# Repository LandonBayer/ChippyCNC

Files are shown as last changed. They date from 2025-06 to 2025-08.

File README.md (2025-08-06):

# Chippy
CNC Mills are expensive, large, and generally not very accessible to the average maker in their home. With Chippy, a small, simple, cheap but powerful CNC router, these capabilities may become available to the hobbiest at a relatively low price. Unlike the commonly found [3018-style](https://a.co/d/4NDyeWJ) cnc, which is a respectable $150 but fails to do anything more than engraving, Chippy boasts linear rails rather than guides, ball screws in place of lead screws, a 500W ER16 spindle, and an extrusion frame to maximize performance. Even the similarly priced Lunyee [3018-pro](https://a.co/d/8d0D7FV) still uses guides and lead screws in place of high quality parts, making Chippy a more compelling DIY package.

I personally had a lot of experience using CNC machines through my robotics team, where I regularly ran an [Omio X8-2200L](https://www.omiocnc.com/products/x8-series/x8-2200l-usb-cnc-desktop-engraver.html) to manufacture parts. Using that experience, I designed Chippy to best compromise performance, ease of use, and reliability in the ways I sought throughout the build seasons. I also did my best to use some parts that I had on hand, such as the linear rails, ball screws (without nuts), a Z stage, and 8020 extrusion. This minimizes my personal input cost, as well as recycles otherwise useless components that I own.

Project Goals:
 - Create a usable but cheap CNC
 - Small footprint (small volume will encompass most parts)
 - Functional speeds, expected to be slow but reasonable
 - Minimum Z probing, ideally X and Y as well
 - Rigid Frame
 - Effective clamping solution
 - Be able to mill aluminum (not just engrave, and not only wood/plastics)

Specs:
- 200 x 180 x 90mm working area (more on the sides for clamping)
- Linear rails to maximize rigidity
- Ball screws to maximize accuracy (not found on any other low cost machines)
- All aluminum frame
- 500 Watt 12000 RPM ER16 spindle
- GRBL Control (outdated but will function perfectly in most scenarios)
- High torque stepper motors on all axis
- Option to switch between a wooden spoilboard for plate work and a machinist vice for 3D parts (note: I can't find exact dimensions on the vice, so that will be added at a later date)
- Integrated E-stop

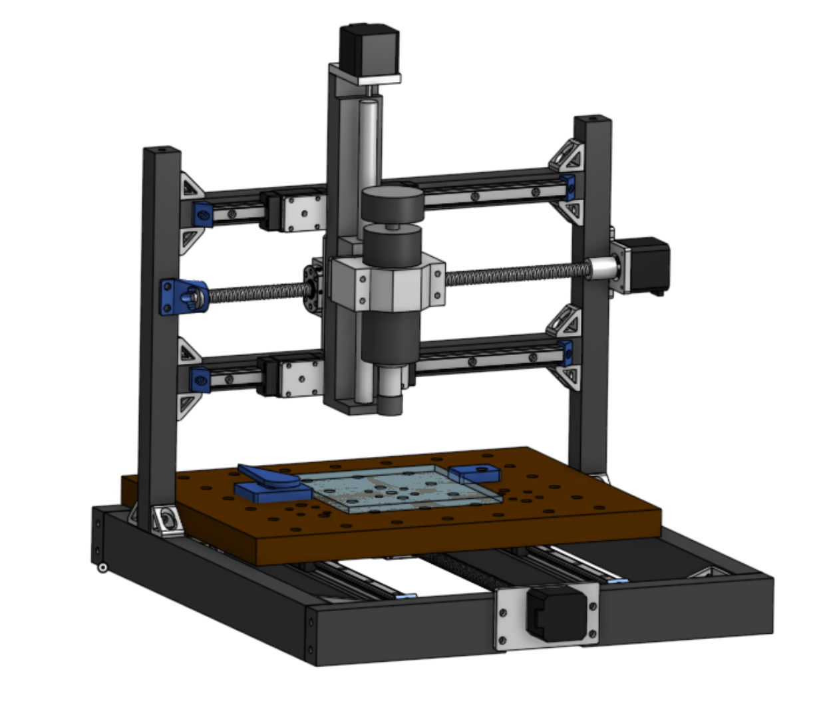
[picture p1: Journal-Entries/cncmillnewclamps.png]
finalscreenshot


[final]: Journal-Entries/cncmillnewclamps.png

[Onshape Link](https://cad.onshape.com/documents/fe491084e56455da2d5a649d/w/3d810b1fec2b376e1d8655d1/e/08e152ea0122b69bfa13cece)

[BOM Link](https://docs.google.com/spreadsheets/d/1udPoCN8MQFdChB4r3Y68Km0VLGHvW1hfCCyUqifvbzs/edit?usp=sharing)

Here's a rough wiring diagram of how to put this machine together, as per Hack Club requirements:

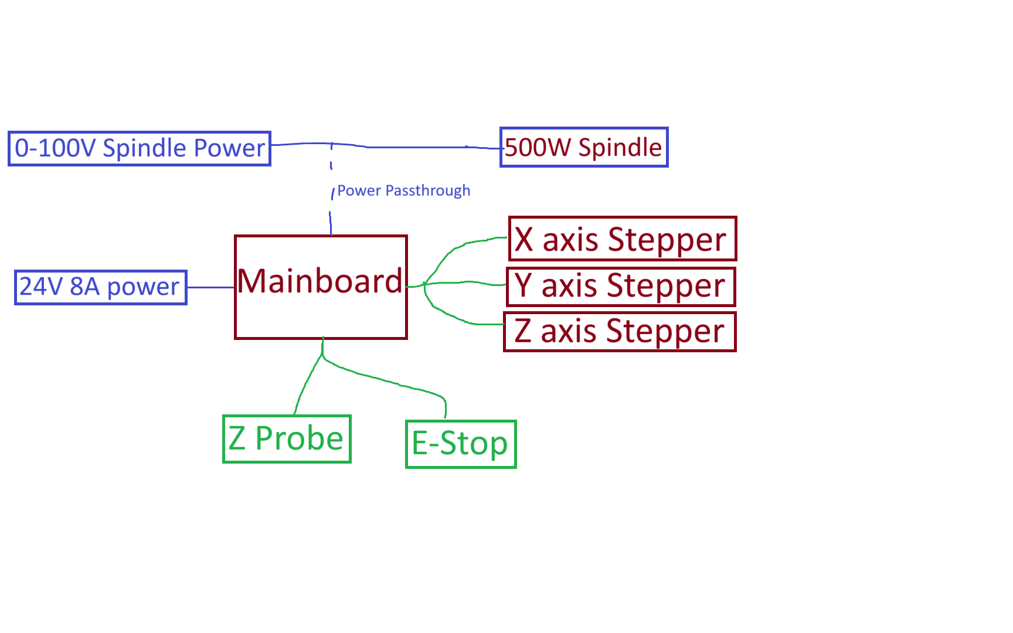
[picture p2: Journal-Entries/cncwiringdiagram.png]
wiringdiagram


[wires]: Journal-Entries/cncwiringdiagram.png

| ITEM | PRICE | QUANTITY | TOTAL PRICE | SOURCE | Ordered | Owned | LINK |
| --- | --- | --- | --- | --- | --- | --- | --- |
| Mainboard | 19.57 | 1 | 19.57 | Aliexpress | FALSE | FALSE | https://www.aliexpress.us/item/3256805662918330.html |
| 400mm ball screw | 22.1 | 2 | 44.2 | Aliexpress | FALSE | FALSE | https://www.aliexpress.us/item/3256802936754324.html |
| ball screw nut mounting block | 4.76 | 2 | 9.52 | Aliexpress | FALSE | FALSE | https://www.aliexpress.us/item/2255800872193882.html |
| Daedalus CNC Spindle Motor Kit, 500w, ER16, Brushed | 99.99 | 1 | 99.99 | Amazon | FALSE | FALSE | https://a.co/d/ilFF7XH |
| 24V 8A power supply (for steppers + control) | 16.99 | 1 | 16.99 | Amazon | FALSE | FALSE | https://a.co/d/3KXWlDU |
| Nema 17 2 amp high torque stepper motors (3 pack) + wires | 32.99 | 1 | 32.99 | Amazon | FALSE | FALSE | https://a.co/d/6JUlACn |
| 5mmx8mm coupler | 6.58 | 1 | 6.58 | Aliexpress | FALSE | FALSE | https://www.aliexpress.us/item/3256807349420029.html |
| Z touch probe | 6.42 | 1 | 6.42 | Aliexpress | FALSE | FALSE | https://www.aliexpress.us/item/3256808663692081.html |
| 3 inch cnc vice + mounting bolts | 44.77 | 1 | 44.77 | Amazon | FALSE | FALSE | https://a.co/d/5kOnS3H |
| E-stop and Limit Switch Kit | 9.78 | 1 | 9.78 | Aliexpress | FALSE | FALSE | https://www.aliexpress.us/item/3256807406356837.html |
| M4 T-nuts for the linear rails (3030 sized work for 1x1 extrusion) | 6.39 | 1 | 6.39 | Amazon | FALSE | FALSE | https://a.co/d/hFEOWDT |
| M10 3pack 25mm pins (for clamping) | 4.9 | 2 | 9.8 | Aliexpress | FALSE | FALSE | https://www.aliexpress.us/item/3256805291847458.html |
| Ball screw support bearings (10mm ID) | 3.32 | 1 | 3.32 | Aliexpress | FALSE | FALSE | https://www.aliexpress.us/item/3256808665674212.html |
| Ball screw support bearings (8mm ID) | 2.99 | 1 | 2.99 | Aliexpress | FALSE | FALSE | https://www.aliexpress.us/item/3256805324873222.html |
|  |  |  |  |  |  |  |  |
| Assorted Metric screws (mostly for M4, I have these already) | 17.83 | 1 | 17.83 | Amazon | FALSE | TRUE | https://a.co/d/3Fa4UwA |
| 90 degree 8020 brackets + bolts (can be used in place of 2x2 ones as well) | 18.9 | 3 | 56.7 | Amazon | FALSE | TRUE | https://a.co/d/7QSxBpf |
| Z stage (recommended 100mm, I had 200mm) | 55.98 | 1 | 55.98 | Amazon | FALSE | TRUE | https://a.co/d/2d2hLF8 |
| 350mm HGH15 linear rails (by far the most expensive part) | 89.92 | 2 | 179.84 | Aliexpress | FALSE | TRUE | https://www.aliexpress.us/item/3256801410951679.html |
| 450mm 2x1" 8020 extrusion (cut to length) | 14.51 | 3 | 43.53 | Other | FALSE | TRUE | https://8020.net/1020.html |
| 450mm 1x1" 8020 extrusion (cut to length) | 9.5 | 2 | 19 | Other | FALSE | TRUE | https://8020.net/1010.html |
| 200mm 2x1" 8020 extrusion (cut to length) | 7.73 | 2 | 15.46 | Other | FALSE | TRUE | https://8020.net/1020.html |
| 400mm 1x1" 8020 extrusion (cut to length) | 8.76 | 2 | 17.52 | Other | FALSE | TRUE | https://8020.net/1010.html |
| 350mm 1x1" 8020 extrusion (cut to length) | 7.97 | 2 | 15.94 | Other | FALSE | TRUE | https://8020.net/1010.html |
| 1kg PLA Pro filament (for clamps and mounting plates if desired) | 24.99 | 1 | 24.99 | Other | FALSE | TRUE | https://us.polymaker.com/products/polylite-pla-pro?variant=39574346334265 |
| 6mm shank 2mm ball NO 3D Probe | 52.35 | 1 | 52.35 | Aliexpress | FALSE | FALSE | https://www.aliexpress.us/item/3256808425022835.html |
|  |  | Necessary total: | 737.82 |  |  |  |  |
|  |  | My total: | 310.6 |  |  |  |  |
|  |  | With probe: | 362.95 |

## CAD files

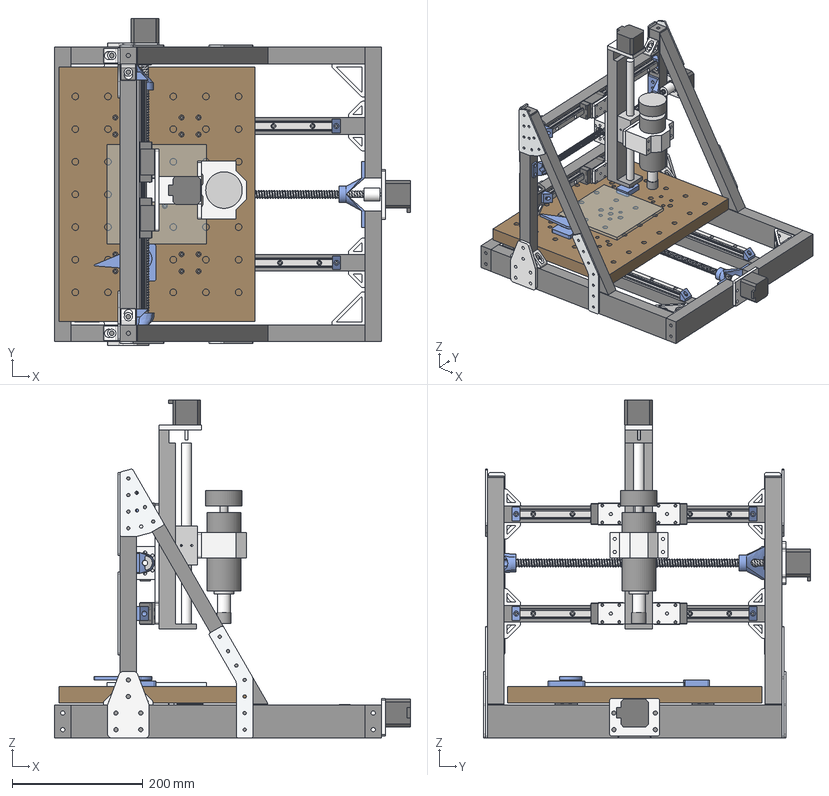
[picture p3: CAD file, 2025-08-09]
CAD-Chippy.step
545.1 x 501.5 x 517.5 mm
Rail End Stop x 8
47065T663_Silver Gusset Bracket x 20
10mm ID Bearing (double) x 2
Y axis rail Extrusion Right
Y axis rail Extrusion Left
X Motor Bearing Support
Base Extrusion Left
Y axis Bearing Support
5mmx8mm Shaft Coupler x 2
Clamping Dowel x 2
2x2 Corner Bracket x 4
Clamping Cam
1 in. 150 Deg. Gusset (am-4165) x 2
Z Mount Plate
Angle Stabilizing Extrusion x 2
NEMA 17 17HE15-1504S v5 x 3
Static Spacer Clamping Block
Spoilboard
1 in. 30 Degree Gusset (am-4160) x 2
Horizontal Extrusion Bottom
Base Extrusion Front Right
X axis Motor Mount Plate
1 in. Tee Gusset (am-4158 ) x 4
Vertical Extrusion Left
Base Extrusion Back
Base Plate Front
Y Motor Bearing Support
400mm ball screw x 2
Ball Screw Nut Housing Block x 2
92029A100 x 8
SFU1204 Nut v1 x 4
X axis Bearing Support
Moving Spacer Clamping Block
Spindle
Spindle Clamp
[Z] HGR15R x 4
[Z] HGH15CA x 8
8mm ID Bearing x 2
Base Extrusion Right
The Mega Z Mount plate
Vertical Rigidity Plate x 2
Vertical Extrusion Right
Base Extrusion Front Left
Stock
Motor Mount (3dp)
Mounting Block
16mm OD ball screw
Horizontal Extrusion Top

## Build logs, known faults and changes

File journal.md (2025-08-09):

---
title: "Chippy CNC"
author: "LandonBayer"
description: "Designing and building a cheap CNC mill using as many random parts I have as possible to minimize cost"
created_at: "2025-05-25"
---
Total time spent: 31 hours

## **5/25/2025 Log 1: Initial Concepts**

I began by trying to figure out if this is even possible. To get my ideas flowing, I made a quick [Google doc](https://docs.google.com/document/d/1eDa18zaTmOcg4O9jXUVwCgunUB5oY8t1EJznX5E89rA/edit?usp=sharing ) with each part of the CNC as I thought of them and explained how I would fulfill that requirement: either with parts I have or links to a cheap option I could use.

I set up this repo, made an [Onshape document](https://cad.onshape.com/documents/fe491084e56455da2d5a649d/w/3d810b1fec2b376e1d8655d1/e/48dd41e2a4bf65c8f3ef253b), and my research document above. I'm doing my best to fit into the $150 price tag to avoid the extra bar for $350 funding, but I may apply for it as necessary in the future. It would certainly be a huge upgrade to the machine, but the goal is a minimum functioning product for as little as possible. 

I'm looking to follow a basic CNC configuration with the spindle moving in XZ and the bed in Y, much like a bedslinger 3D printer or a 3018 style CNC.  

Time Spent: 45 Minutes (mostly research)

## **5/25/2025 Log 2: Ideation**

Some parts are not in my house at this exact moment so I need to wait a few days to go and grab them. In the meantime, I'll try to design most of the printer and be able to swap out the CAD models as I get the real ones and create/find models for them.

It is also worth noting that I have access to an Omio CNC router through my robotics team, which will enable me to make custom parts in aluminum or polycarbonate as I please (though I may have to buy stock as part of my budget). I also recently set up a 4th axis on it, so I can even do some more complex parts too.

Here are some sources of inspiration:

Cubiko CNC
3018 CNC

Time Spent: 15 Minutes

## **5/26/2025 Log 3: More Research**

I can't get some of the parts that I need until tomorrow, so I'm mostly holding off on CAD work until then to avoid extra work. In the meantime, I'm continuing to look into how I'm going to put this all together. I'm currently examining [GRBL-Mega](https://github.com/gnea/grbl-Mega), since I have an Arduino Mega with some sort of motor driver hat that hopefully is compatible. I also have a random Raspberry Pi 3B that I could use as a standalone computer for the CNC (just so it doesn't have to sit next to my real computer).
I'm doing as much pre-requisitve research as possible while I wait for those parts and so I don't waste time doing something that isn't possible (or I know where to put more of my budget). So far, the main budget items I have planned for are a spindle (cheapest one I could find is $27, the 3018 type spindle with an ER11 collet), a fixture table that I will likely make myself on the Omio CNC, stepper motors, and possibly a second ball screw of the same model I already have (~60, comes with a motor). Again, I'm hoping to stay under $150 but I may expand beyond that to accomodate any necessary parts for the functioning of the machine, or add more features like probing, an enclosure, or a better spindle.

Time spent: 45 Minutes

## **6/02/2025 Log 4: Finding Parts**

Most of this past week, I've been busy with the end of the school year, but I still took some time to get together all the parts I currently have and what needs to be purchased. To recap, I have two 400mm ball screws without nuts, four 350mm HGH15 linear rails, a RATTMMOTOR CBX 1605-200mm Z axis without a motor, and have since determined that the Arduino Mega with the Reprap RAMPS V1.4 sheild I have will not work as it is more suited for 3D printers and doesn't have the power to run a spindle. With these decisions, I am currently leaning toward [this](https://www.aliexpress.us/item/3256805662918330.html) control board, two of [these](https://www.aliexpress.us/item/3256807902881311.html) ball nuts, and finally [this](https://a.co/d/bSWRW8X) power supply and spindle combo, which I know will be compatible with the chosen control board.

parts I have

[parts]: Journal-Entries/parts.jpg

Of these, my biggest concern is the spindle, as it is quite small and has a high risk of lacking rigidity. I really just want this to function, so even if it is very slow or only mills soft materials, I'll be happy and can expand upon it later. The total cost for these parts is around $105, leaving me only $45 left in my budget to purchase any other components like the stepper motors, structural hardware, limit switches, wiring, and other necessary components like shaft couplers, bolts, etc. Because of this, alongside the potential for a significantly more powerful machine by spending just slightly more, I am likely going to propose my project to the $350 budget range in order to make this viable.

Time spent: 1 hour (over the week)

## **6/03/2025 Log 5: Beginning Design**

Given that I'm starting with many parts on hand, I'm getting 3D models of them where possible. I was able to find a model for the [spindle](https://www.thingiverse.com/thing:4856147), [linear rails](https://grabcad.com/library/hgh15ca-hgr15r-1), and [ball screw nuts](https://grabcad.com/library/sfu1204-ballscrew-nut-22mm-1). I also whipped up a model for the lead screw in Onshape using a helix curve and a sweep toolpath with a 2.5mm circle and a 5mm pitch helix. Unfortunately, this mainly leaves the Z stage without a model, of which I may need to replicate myself. To minimize the amount of CAD work to be done, I only plan to model the block (nut) on the screw, since those mounting features are the only part of the assembly that I really care about, alongside the back of it which has rails with captive nuts for mounting. With these parts accounted for, I'll now move into more modeling of the machine, based around a few design constraints: the parts I have, using 8020 for structural pieces where possible, and doing any custom parts based on 1/4" plate as I have access to it in small quantities.

Separately, I've tentatively decided on [this](https://a.co/d/2pTGfU2) 3-pack of NEMA 17 stepper motors that should be compatible with the control board as well and are quite cheap at $26 for all three. I have added the associated [3D model](https://grabcad.com/library/nema-17-17he15-1504s-1) to my Onshape document as well.

Time spent: 1 hour

## **6/04/2025 Log 6: Base sketches**

I did out some sketches in Onshape, making this as parametric as possible. I'm using some variables to name certain values like the length of my rails, ball screws, and the gap between the table and the spindle (Z-gap). I'm taking the time to think through these sizes and constraints to ensure they will propogate down correctly later on if I need to change things. I also made a small subassembly for the linear rails with limited slider mates on the blocks.

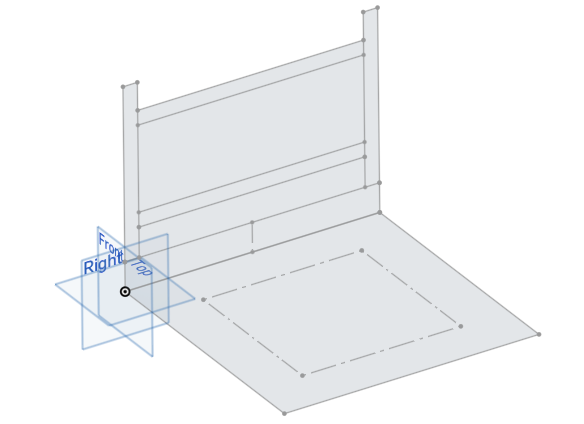
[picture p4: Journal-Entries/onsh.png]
onshape


[def]: Journal-Entries/onsh.png

Time spent: 30 minutes

## **6/16/2025 Log 7: More Onshape**

I worked out the back of the mill, which is the X axis and will hold the Z axis on it. I'm starting very simple, with some 8020 extrusions going around and some 2x1 ones at the bottom to give me some space for the rails and ball screw on the Y axis. My main issue with this was that the 8020 featurescript in Onshape is really difficult to use, as it generates facing straight up all the time. I spent quite a while trying to figure out a workaround and eventually settled on a not-ideal but somewhat parametric way to get the lengths set in the part studio.

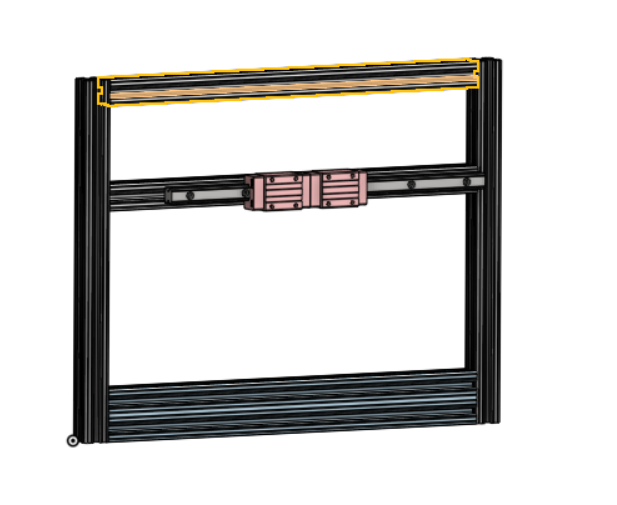
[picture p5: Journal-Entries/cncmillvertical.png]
cncmillvertical


[vert]: Journal-Entries/cncmillvertical.png

Time spent: 1.5 hours

## **6/17/2025 Log 8: Onshape Struggles Continue**

As I build out the rest of the machine in Onshape, I am beginning to really hate the 8020 featurescript and even using it as a part in CAD. Since it has rounded corners, I cannot add mate connectors to the corners exactly and instead have to use some strange face mates to connect the pieces. After discussing these issues with another Hack Club member, he recommended I simply model the 8020 as a solid 1x1 inch box, which I will convert now before the design gets too large. This means I will basically have to re-do both the part studio and assembly, but it will make things much easier going forward. You can also see some corner braces and attachment methods being added, though they aren't completely cadded in yet. I have some small 1x1 corner brackets, large 2x2 brackets for the inside of the base, and square pieces that are meant to attach three tapped 8020 extrusions in the corners (more details to come). Let's get to the conversion!

Before pic:

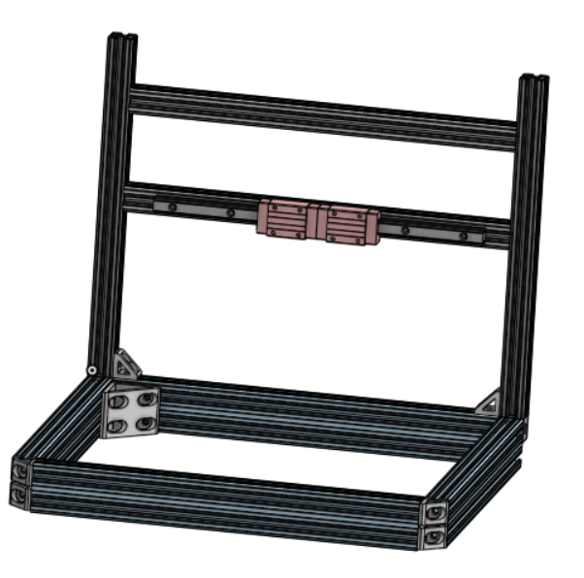
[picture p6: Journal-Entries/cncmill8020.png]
cncmill8020


[eightytwenty]: Journal-Entries/cncmill8020.png

Time spent: 1 hour

## **6/18/2025 Log 9: Onshape grind + Rethinking the machine**

I'd like to touch on that rethinking part first: I was initially trying to hit the $150 price point Hack Club offers, but after reviewing the guidelines more closely, I believe this is likely to fall into the advanced $350 category. For this reason, I'm looking at possible changes to my spindle (easiest) or even to the control board, drivers and motors (harder). The spindle is a straightforward upgrade with the same controller up to a 500W spindle, which makes it an ideal easy solution. However, the main limiting factor at this point would be the stepper motors I'm using to drive the whole machine, which are limited to 2 amps of maximum current based on the A4988 drivers the control board has. If I choose a different control board without integrated drivers, I could increase the power of those drivers up to 4A or higher, giving me room to put on larger stepper motors that will make the machine run much better. I will be continuing to consider this option as I move forward with the design, as it should not be heavily reliant on this choice.

As for Onshape, now comes the time to re-do all the 8020 extrusions to be simple boxes for ease of design. Here is what it looks like after:

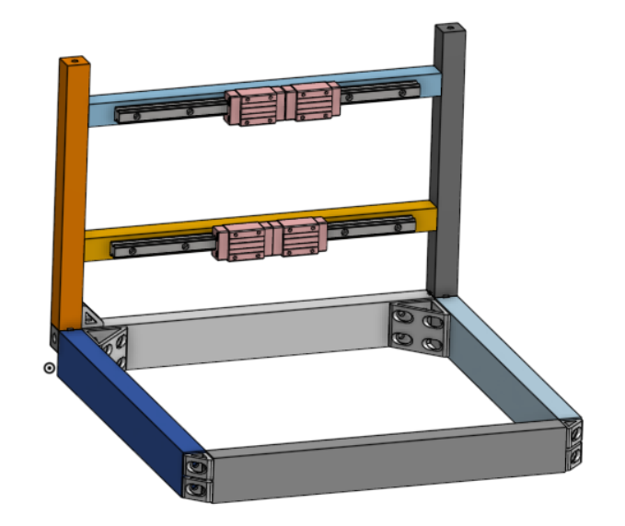
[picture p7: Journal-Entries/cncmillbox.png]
cncmillbox


[box]: Journal-Entries/cncmillbox.png

Naturally, after doing all of this, I began rethinking my work from the start. I'm now realizing it could be easier for the operator (myself) to use if the bed is completely stationary and the spindle moves in XYZ, much like a typical cnc router. I will also be considering this as I continue working, and might create a branch in Onshape to test this out if it appears to be desirable. I am still unsure how this would complicate or simplify my ability to move each axis with the ball screws, which I am yet to figure out exactly in either design. I may replace some 8020 sections with 1/4" sheet aluminum milled to my specifications (on the router I have access to). This is likely to be more expensive, but may produce better end results.

Time spent: 1.75 hours

## **6/19/2025 Log 10: Big progress**

Today I really locked in on cad and got a lot done, fixing many issues and continuing the design phase. After much thought, I stuck with the bedslinger style of kinematics (XZ on the head, Y on the bed), but realized that the XZ section must be centered on the mill to reach all of the millable area. I also replaced the front and back of the machine with 1/4" aluminum plate that I will mill out, simplifying the design by allowing me to easily mount the motor that drives the Y axis (pictured in the grey motor below). That said, I'll probably re-do it again to have a smaller mounting plate because that one is massive and impractical.

I continued at sorting out the core kinematics, first by adding some 40-1620 8020 extrusion as a bed to the printer. My hope is that this will make it easy to clamp parts and add a spoilboard on top. The main downside is cost, at a whopping $60 for the build plate pictured. I will keep in consideration another spoilboard mounting solution as well as possibly some way to add a machining vice for larger 3D milling operations (possibly a way to detach the bed and add a vice directly to the linear rails?)

As you can see, I got around to creating a 3D model of my [Z axis](https://a.co/d/2vU4E41) to continue figuring out my placement for the spindle motor and X axis power. In an ideal world, the X axis ball screw could run between the rails, just behind the Z axis assembly to increase rigidity. Doing so may require some kind of custom motor mounting plate, which is certainly fine within the scope of this project.

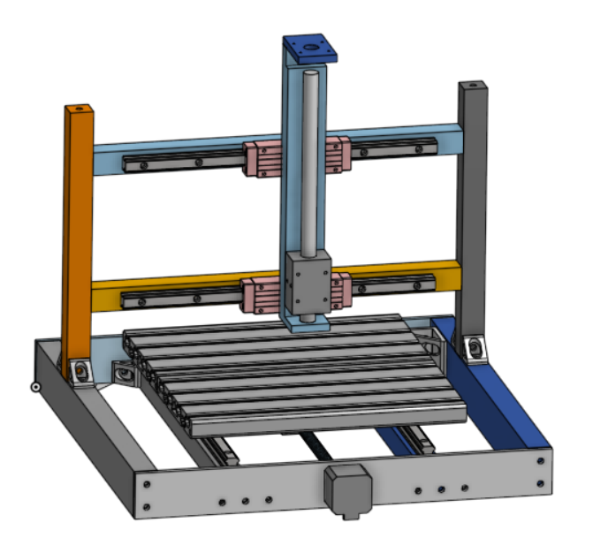
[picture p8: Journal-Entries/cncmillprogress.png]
cncmillprogress


[prog]: Journal-Entries/cncmillprogress.png

Time spent: 3 hours (honestly much more but let's just count 3)

## **6/20/2025 Log 11: Keeping it Moving**

I redid the front and back again to use smaller milled plates, though I may even make the back a single piece of extrusion as it isn't entirely needed. I got around to creating models for the spindle and the clamp it comes with, which will need some kind of adaptor plate to the Z axis. I'm getting relatively close to a point where I can begin ordering parts (aka submitting to HC), so I'm super excited for that! The major tasks that remain are the X axis power, creating various mounting plates and adaptors, and sorting out smaller details like modeling in bolts where needed, adding shaft collars to the motors to connect the ball screws, etc. I already have most of my plans sorted out for the controls and such, which aren't currently modeled as it doesn't really make a functional difference just yet. Here's the progress photo for today:

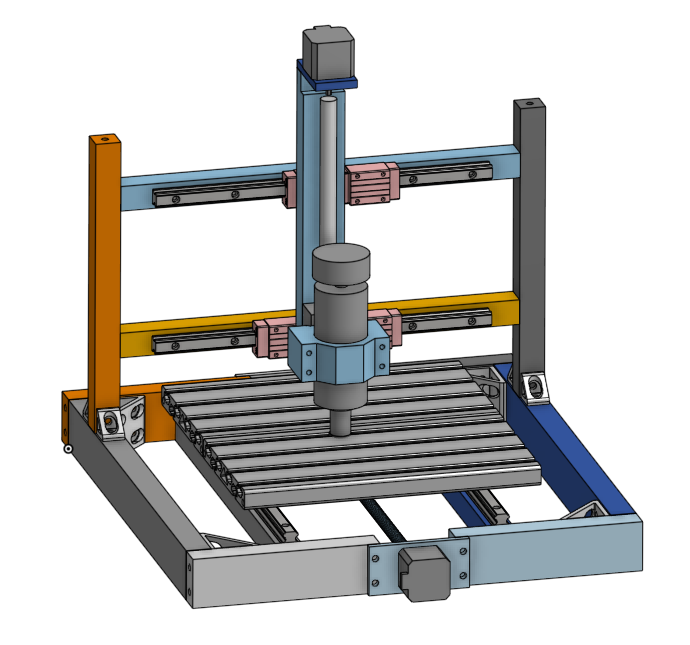
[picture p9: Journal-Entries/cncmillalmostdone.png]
cncmillalmostdone


[almost]: Journal-Entries/cncmillalmostdone.png

Time spent: 1.5 hours

## **6/27/2025 Log 12: Tidying Up Loose Ends**

This log will cover the small pieces I've been doing over the course of that last week (I've been busy so it's all clumped together). First, I found that I can buy ball nut housings for quite cheap, giving me a strong aluminum connecting piece for X and Y power. However, the threads they come with don't match perfectly with my other parts so some adaptor plates were made too. Here's one of them on the X axis power:

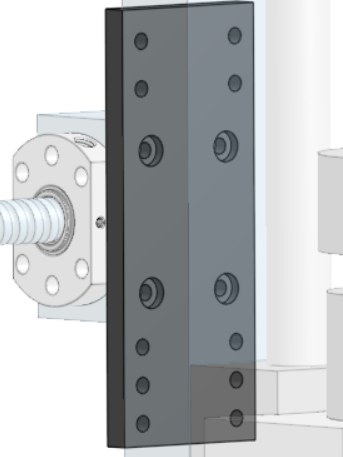
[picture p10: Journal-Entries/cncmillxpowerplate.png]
cncmillxpowerplate


[powerplatex]: Journal-Entries/cncmillxpowerplate.png

The pockets are countersinks for the bolts going into the block, while the holes above and below are for the slots on the Z axis. 

I also made some plates to mount the X axis rails to the Z axis, which are nice and simple: they keep the two carraige blocks close as to minimize any reduction in travel distance while also maintaining rigidity. I will do the same for the Y axis soon. Here's what those look like:

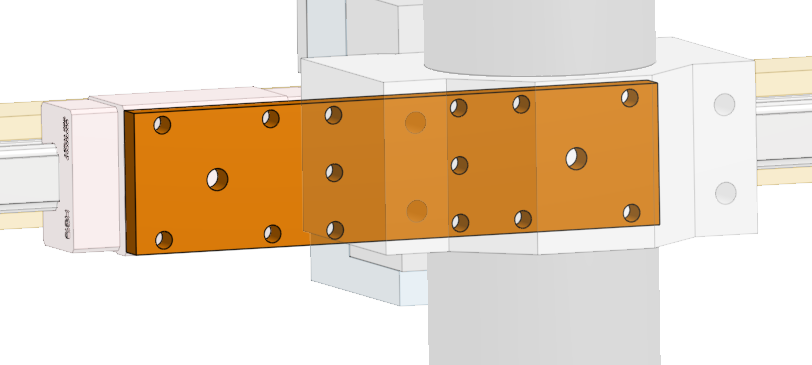
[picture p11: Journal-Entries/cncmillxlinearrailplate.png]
cncmillxlinearrailplate


[linearrailx]: Journal-Entries/cncmillxlinearrailplate.png

Here's what the full assembly looks like at the moment (note: the X axis motor plate is modeled but not in the assembly yet):

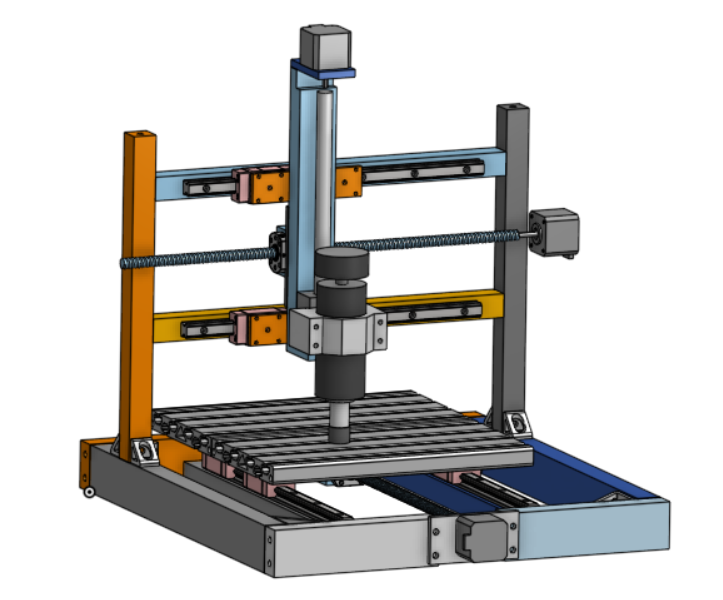
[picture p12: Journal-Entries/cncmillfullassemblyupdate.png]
cncmillfullassemblyupdate


[fullassembupd]: Journal-Entries/cncmillfullassemblyupdate.png

Of course, there are still many small pieces to figure out! One big thing is changing out the bed: I want to change it from that extrusion (very expensive for what it is imo) to a simple spoilboard (which I need anyway). This way, I can simply have holes drilled to bolt directly to the linear rails and the ball screw (no adaptor plates), as well as some kind of hole-based clamping system [like this one](https://youtu.be/O-rqf4uSXRE?si=c4zoKhAtzv9de5E1). I also need to make 3D printed end stops to the rails, 3DP parts with bearings to hold the ends of the ball screws, and some other final touches. Looking forward to finishing this off!

Time spent: 2 hours

## **7/11/2025 Log 13: Final Log!**

We're just about finished and ready for submission to Hack Club! First some updates since the last note:
- Switched to the spoilboard base as planned for cost reasons
- Re-did the colors in Onshape to look nicer and be more informative by material
- Created the spoilboard clamping system as a clone of [Marius Hornberger's design](https://youtu.be/O-rqf4uSXRE?si=c4zoKhAtzv9de5E1), using 3D printed cam clamps (may be adjusted if too weak in the future)
- Completed the [BOM](https://docs.google.com/spreadsheets/d/1udPoCN8MQFdChB4r3Y68Km0VLGHvW1hfCCyUqifvbzs/edit?usp=sharing) with all parts needed for construction

With these, I'm calling the project done! I may need to make some minor adjustments later on as I run in to issues and such, but for the time being it's all set. Thank you for reading and to Hack Club for providing this opportunity!

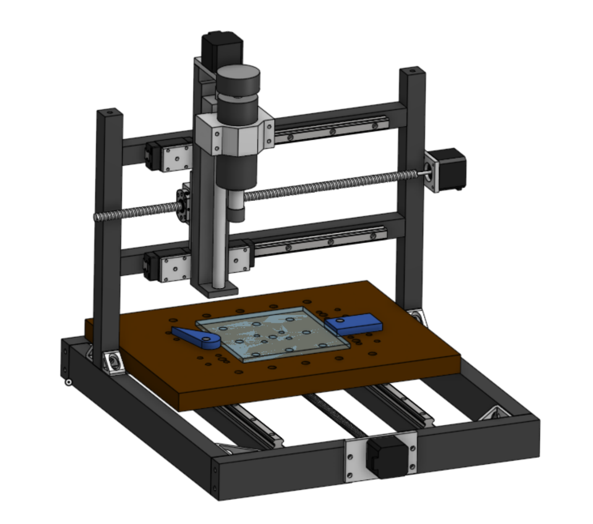
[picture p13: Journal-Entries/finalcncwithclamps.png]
finalscreenshot


[final]: Journal-Entries/finalcncwithclamps.png

Time spent: 5 hours (mostly finishing BOM and writing this/the readme)

## **7/12/2025 Log 14: Oops not final log**

Well, I realized I was certainly not ready for my actual submission, as this has to be 100% fleshed out before review. First, I made a relatively large change to the printer by choosing to purchase ball screws as it costs a total of $20 more and my current ones don't appear to be a standard size. I don't believe it is worth the risk to buy ball screw nuts only and pray they fit the ones I have. Instead, I'll be purchasing 400mm ball screws with machined ends down to 8mm (allowing me to use 5mm to 8mm couplers), spending a bit more but preventing a possible failure of the project. This change also made the extrusions standard sizes of 450, 400, and 350mm across the board, which honestly doesn't make a huge difference as they must be bought cut or cut yourself regardless, but it's a nice addition. To touch up everything, I added 3D printable end stops to the linear rails to prevent them from falling apart, modeled in the shaft couplers, and added 3D prints and bearings to the ends of the ball screws to ensure they are supported. 

newclampsinassembly

[newclamps]: Journal-Entries/cncmillnewclamps.png

I also began printing out some parts to check their compatibility and function, as well as a simple test jig for my clamping method. When holding the lever, the clamp is quite strong, but it seems to naturally fall back to a rest (no force) position when letting go. Based on the video from above, the original creator mentioned that the travel on his clamps was "12mm" which is "quite a lot". Mine currently are modeled as 13.75mm of travel (a specific size based on my hole spacing, which I will change after seeing it in real life regardless), and my clamps seem to be significantly smaller overall as well. Because of this, I designed a version with significantly reduced travel distance to apply a larger force. I thought I could get away without having spacer blocks on the cam lever, but now realize that is part of what allows you to get greater pressure on the clamp. Here's a picture of how my old model looks in real life: 

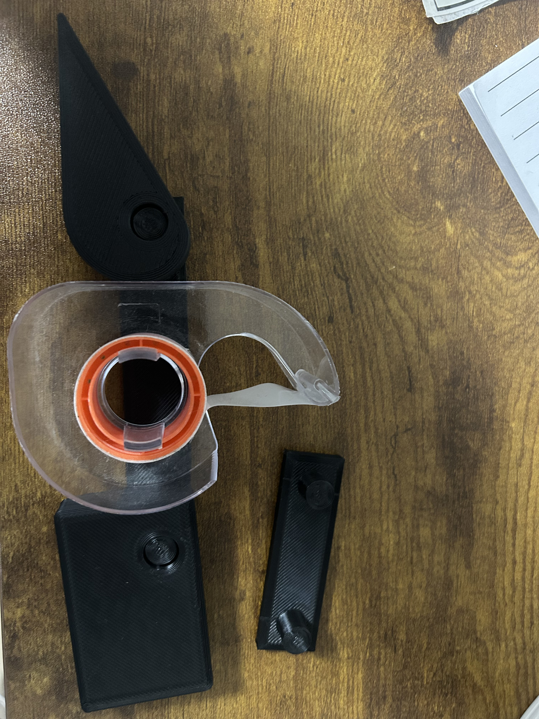
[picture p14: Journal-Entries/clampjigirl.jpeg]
clampsirl


[clampsirl]: Journal-Entries/clampjigirl.jpeg

I will soon print out a new test jig with the new clamp style and see how it fares. Hopefully all goes well! Other than refining this, I believe pretty much everything is set on the design front for now. I could add some kind of enclosure, but that's a project for another day as it definitely won't be in the budget :)  I went ahead and updated my BOM to match all my changes, and I'm looking forward to actually being done soon!

P.S. the new clamp style worked!! Here it is holding another plate quite securely. That spacer block and lower travel was the trick!

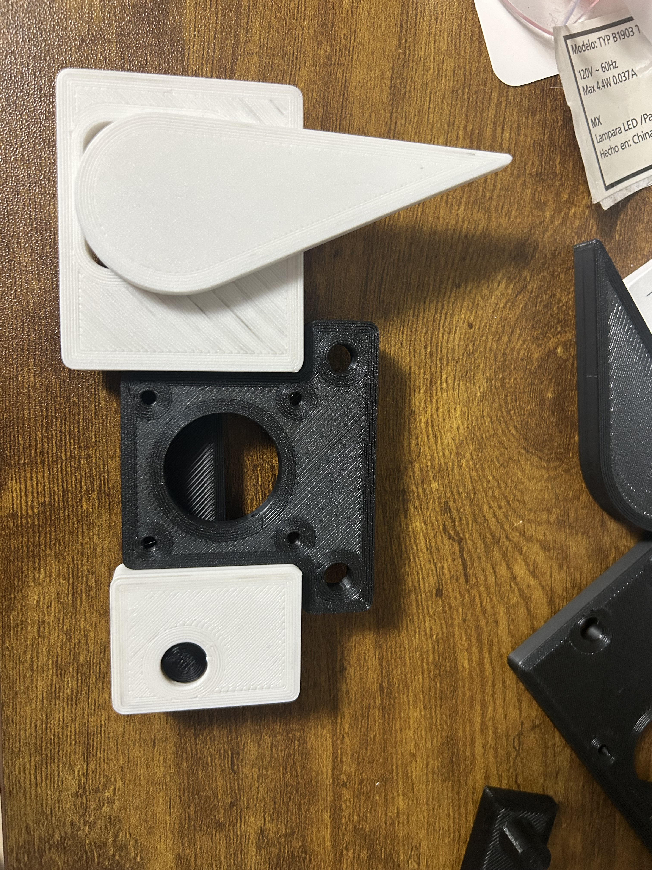
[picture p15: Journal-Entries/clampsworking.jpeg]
clampsirlworking


[clampsirlwork]: Journal-Entries/clampsworking.jpeg

Time spent: 6 hours

## **7/17/2025 Log 15: Actual final log until revisions**

I already submitted this project and am awaiting review, but I quickly added in a scaled down model of a typical CNC style vice to approximate what my real one would look like (since no dimensions were given). I did so by finding a similar looking model online and scaling it down until the hard jaw was 3 inches across, as mine would be, and just eyeballing the slot positions compared to the provided images seemed about right. I made a fixture plate to attach it so that I can switch between using the spoilboard and the vice, and added Onshape configurations to reflect this idea. Here are the two setups:

Spoilboard:

spoilboardversion

[spoil]: Journal-Entries/cncmillnewclamps.png

CNC vice:

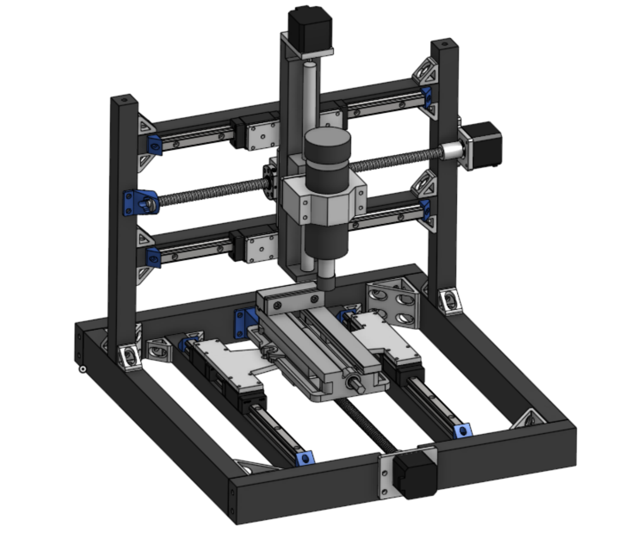
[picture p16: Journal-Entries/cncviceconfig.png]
viceconfiguration


[vice]: Journal-Entries/cncviceconfig.png

Time spent: 1 hour

## **8/5/2025 Log 16: Post review Log**

In my review, the main concern was simply rigidity: I designed an all aluminum extrusion frame, since I simply have it, but the reviewers were concerned this may not prove rigid enough for CNC, at least in the small pieces going up to the X and Z axis. To rectify this, I added some slanted braces of extrusion and many more gussets (both off the shelf and custom) to these areas. I also combined the 3 Z axis plates on the rails and ball screw into one mega-plate, hopefully increasing the rigidity of that setup as well. The plate is still reasonably small enough to machine, which was my initial concern in doing so.

The best part? All of these modifications barely increase my total, as these are also parts I have access to (the gussets and such). The bearings for the motor-side supports must be 10mm ID instead of 8mm so those have to be added on, but that should be a small cost compared to the overall machine.

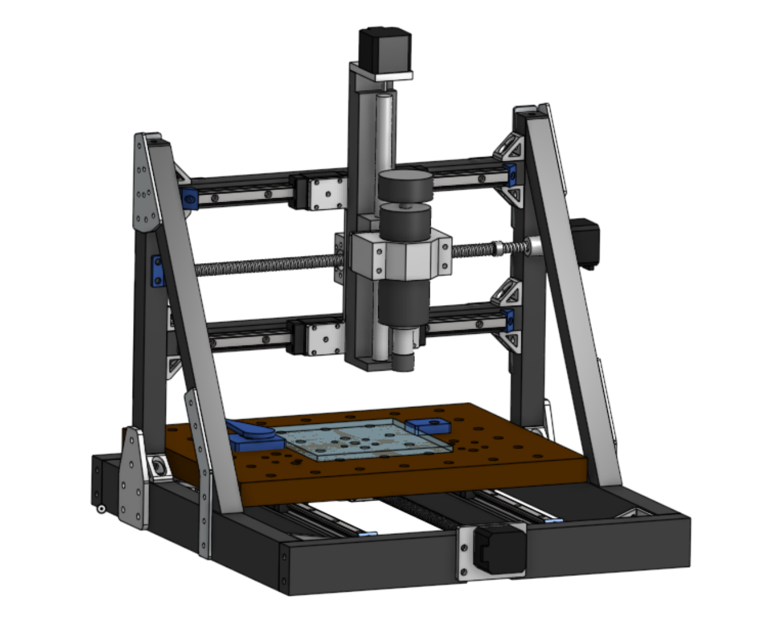
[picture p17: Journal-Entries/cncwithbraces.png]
front


[front]: Journal-Entries/cncwithbraces.png

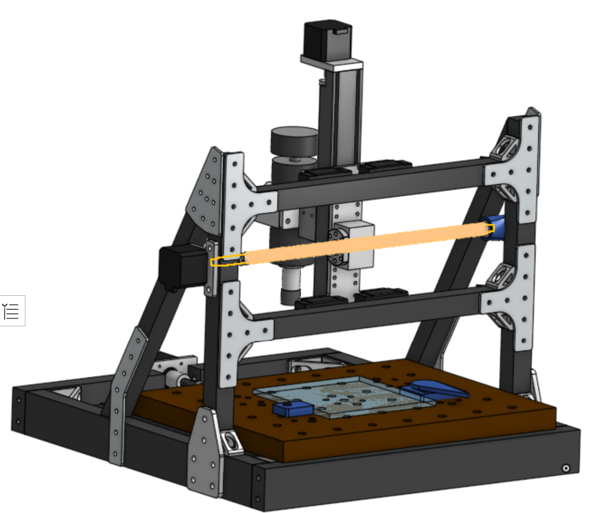
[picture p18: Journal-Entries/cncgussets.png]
back


[back]: Journal-Entries/cncgussets.png

Time spent: 3 hours

## **8/9/2025 Log 17: Quick post review edits (waiting for rereview)**

I added in the 3D printed bearing mounts for the motor side pillow bearings, which are meant to add rigidity to the ball screws and reduce play. The parts are 3D printed, so the increase may me somewhat minimal, but something is better than nothing and ideally it will reduce the load on the motor shaft and therefore internals of the motors, making them last longer. Here are screenshots of each of the mounts (zoomed out for context): 

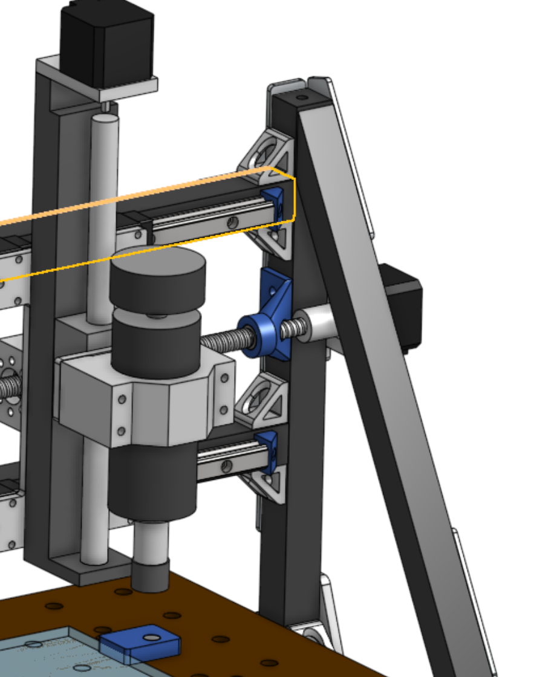
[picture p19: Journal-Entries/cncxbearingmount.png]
xbear


[xbear]: Journal-Entries/cncxbearingmount.png

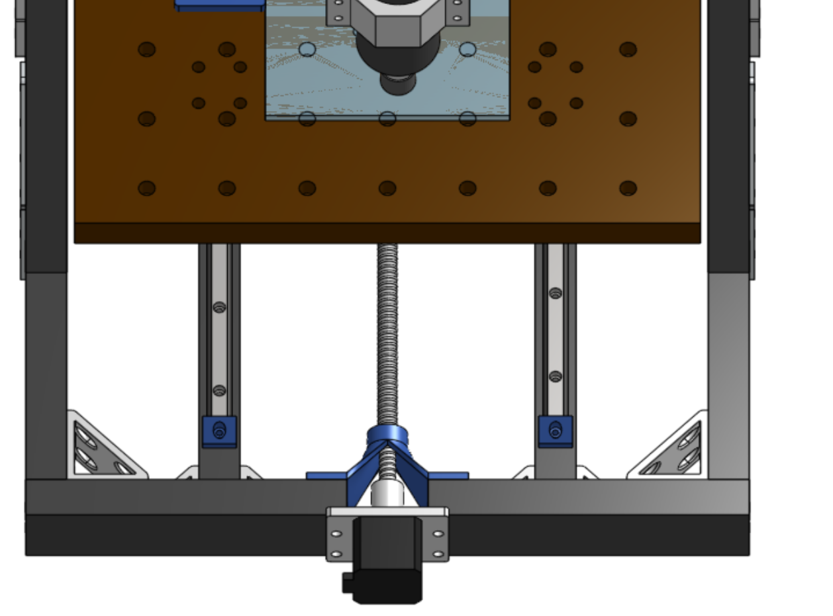
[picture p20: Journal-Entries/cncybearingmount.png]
ybear


[ybear]: Journal-Entries/cncybearingmount.png

And a final image:

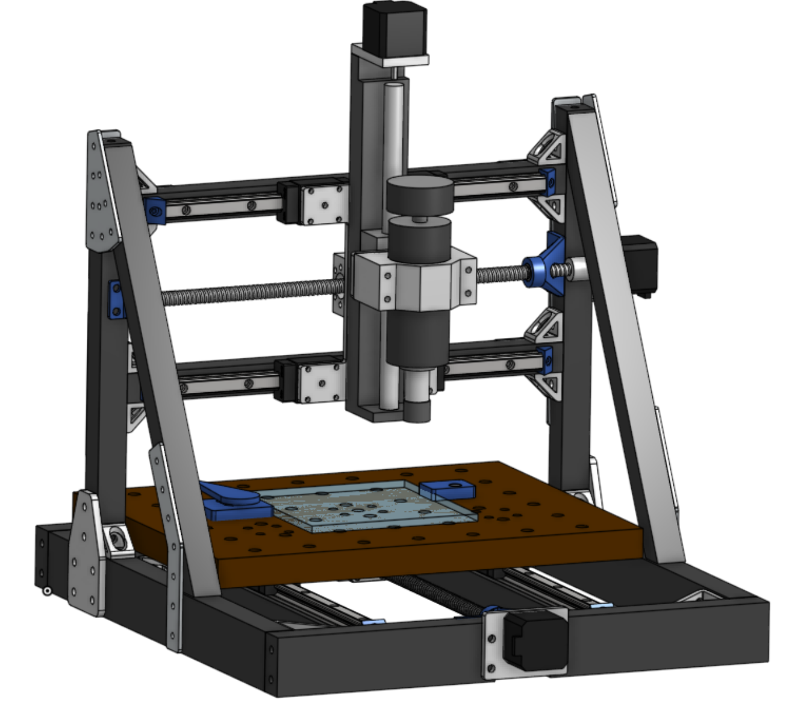
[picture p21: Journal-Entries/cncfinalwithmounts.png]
finfin


[finfin]: Journal-Entries/cncfinalwithmounts.png

Time spent: 1 hour

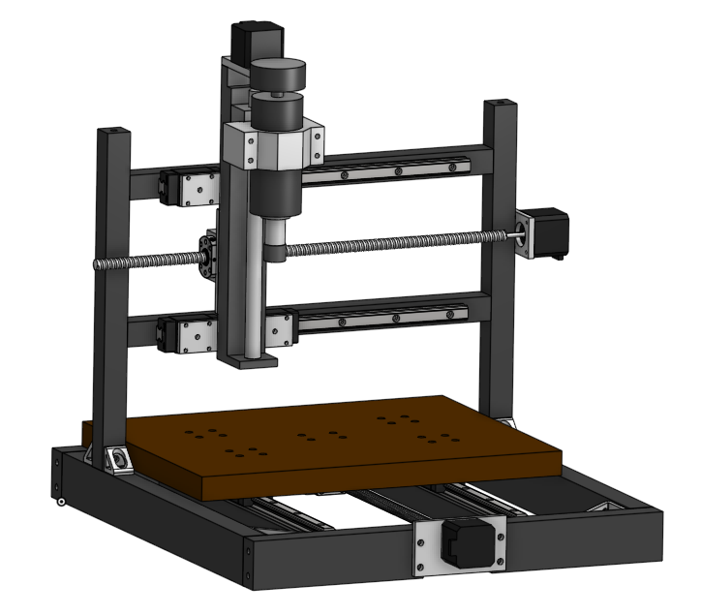
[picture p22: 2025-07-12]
Journal-Entries/finalCNCscreenshot.png

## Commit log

2025-07-12 Semifinal Commit (reorganize, update readme and journal, etc)
    [CNC Mill BOM - BOM.csv]
2025-07-12 Another semifinal commit
    [CNC Mill BOM - BOM.csv]
2025-07-12 wiring diagram
2025-07-12 updating bom
    [CNC Mill BOM - BOM.csv]
2025-07-14 another log update and file update
    [CNC Mill BOM - BOM.csv]
2025-08-06 re review commit
    [CAD-Chippy.step]
2025-08-09 final pre-rereview commit
    [CAD-Chippy.step]
